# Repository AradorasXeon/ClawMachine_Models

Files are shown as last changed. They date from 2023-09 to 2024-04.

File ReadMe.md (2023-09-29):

Models are made in SCAD, STLs are also generated there.

GCodes are generated with Cura for ENDER3 printer (not V2, not some fancy version, but probably would work on any of those).

License: MIT License

Copyright (c) 2023 Krisztián József Varga

Permission is hereby granted, free of charge, to any person obtaining a copy
of this software and associated documentation files (the "Software"), to deal
in the Software without restriction, including without limitation the rights
to use, copy, modify, merge, publish, distribute, sublicense, and/or sell
copies of the Software, and to permit persons to whom the Software is
furnished to do so, subject to the following conditions:

The above copyright notice and this permission notice shall be included in all
copies or substantial portions of the Software.

THE SOFTWARE IS PROVIDED "AS IS", WITHOUT WARRANTY OF ANY KIND, EXPRESS OR
IMPLIED, INCLUDING BUT NOT LIMITED TO THE WARRANTIES OF MERCHANTABILITY,
FITNESS FOR A PARTICULAR PURPOSE AND NONINFRINGEMENT. IN NO EVENT SHALL THE
AUTHORS OR COPYRIGHT HOLDERS BE LIABLE FOR ANY CLAIM, DAMAGES OR OTHER
LIABILITY, WHETHER IN AN ACTION OF CONTRACT, TORT OR OTHERWISE, ARISING FROM,
OUT OF OR IN CONNECTION WITH THE SOFTWARE OR THE USE OR OTHER DEALINGS IN THE
SOFTWARE.

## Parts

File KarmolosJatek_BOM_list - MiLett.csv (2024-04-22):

 |  | Honnan Rendeltem | Megnevezés | Link | Méret ha van | DB szám
Egy csomó szerszámot is vettem, de ezeket későbbi projektekhez is részben, csak sok volt, ami most kellett először, azokat nem listázom ide. |  | Model elveszett | X_tarto-Y-kocsira | 3D nyomtatni |  | 1
Ezenkívül voltak dolgok, amikből többet vettem, de a darabszámnál a felhasznált mennyiség került feltüntetésre, az árhoz azt írtam be, amibe nekem megrendeléskor az adott mennyiség került. |  | Model elveszett | X_tarto-Y-tengelyre_LM8uu | 3D nyomtatni |  | 1
Figyelembe véve a projekt hosszúságát, és hogy mennyire későn kezdtem neki ennek a BOM listának, a dokumentáció nem teljes körű. Itt ott kisebb nagyobb eltérések lehetnek benne. |  | Model elveszett | TekercseloMOtorTarto | 3D nyomtatni |  | 1
 |  | Model feltöltve | TekercseloTarcsa | 3D nyomtatni |  | 1
árak (2023.09.16) rendeléskor februárban lehet olcsóbb volt... |  |  |  |  |  | 1
 | 4 017 Ft | OBI | MDF lap 8 mm (hátlap) | 0,59075 | 850x695 | 1
 | 3 361 Ft | OBI | MDF lap 8 mm (top box alja) | 0,4942 | 700x706 | 1
 |  | OBI | HDF fedo 8 | 0,42575 | 650x655 | 1
 | 3 270 Ft | OBI | MDF alja + legalja (300×261) 8 | 0,48094 | 692x695 | 1 | Ez végül külön tétel volt, bár az egyik kivágást én csináltam
Sajnos nem találom a weblapon már a konkrét típust, de ha jól emlékszem ez már akkor se ment 3500 Ft/m körül mozgott az ára, ha jól emlékszem + vágás díja volt, 3600 / m-rel számolok |  | OBI | Deszka (20x100) | 2,8 | 700 | 4
 | 9 504 Ft | OBI | Deszka (20x100) | 2,64 | 660 | 4
 | 1 566 Ft | OBI | Deszka (20x100) | 0,435 | 435 | 1
 | 1 019 Ft | OBI | Deszka (20x100) | 0,283 | 283 | 1
 | 2 408 Ft | OBI | Deszka (20x100) | 0,669 | 669 | 1
 | 997 Ft | OBI | Deszka (20x100) | 0,277 | 277 | 1
 | 1 328 Ft | OBI | Deszka (20x100) | 0,369 | 369 | 1
ennek anno felírtam h 38 ezer a kettő együtt | 17 717 Ft | OBI | Plexi | https://www.obi.hu/muanyag-tetok/gutta-lemez-2-5-mm-polisztirol-sima-200-cm-x-100-cm-atlatszo/p/3230216 | 700x850 | 3 | front az 1-ikből vágva | https://www.obi.hu/muanyag-tetok/gutta-lemez-2-5-mm-polisztirol-sima-200-cm-x-100-cm-atlatszo/p/3230216 | ez: 1*2 m-es verzióban | vastagság: 2,5 mm |  | =>9,2 kg
De kivágások miatt ebből úgyis kell 2 db |  | OBI | Plexi |  | 263x142 | 1 |  |  | ebből 2 db kellett ~38 000 Ft
 |  | OBI | Plexi |  | 300x142 | 1
 | 11 200 Ft | OBI | L profil 2020x10 |  | 1000 | 8 |  | https://www.praktiker.hu/csavar-zar-vasalat/vasalat-profilos-anyag/lemez-profil-szogvas/308666-dinocoop-l-profil-20x20x1-0-1m-szimmetrikus-alu-nyers | Ez kiderült, hogy van az OBI-ban is, csak én nem találtam valahogy, eredetileg 4 db volt az oszlophoz, de akkor még nem tudtam, hogy lehet hosszabb kiszerelésben is venni, akkor már olyanra csináltam volna, hogy teljesen végig érjen. A végeredmény azt hiszem 8 db 1 m-es volt, a 4 oszlopon kívül még ment a kiadó nyílsához kívülre és belülre is, illetve a plexi felső része is ragasztva lett ilyennel.
 | 560 Ft | OBI | Sarok Vas 2020 |  |  | 8 |  | https://www.obi.hu/sarokoesszekoetok-faoesszekoeto-vasak/szekszegletvas-sarga-horganyzott-25-mm-x-25-mm-x-14-mm/p/3098407
 | 256 Ft | OBI | HDF Irányító doboz (6 mm) | 0,05694 | 438 x 130 | 1 | teteje
 | 202 Ft | OBI | HDF Irányító doboz (6 mm) | 0,044928 | 432 x 104 | 1 | szemből lap
 | 57 Ft | OBI | HDF Irányító doboz (6 mm) | 0,01261 | 130 x 97 | 1 | jobb lap
 | 58 Ft | OBI | HDF Irányító doboz (6 mm) | 0,012896 | 124 x 104 | 1 | bal lap
 | 199 Ft | OBI | HDF Irányító doboz (6 mm) | 0,044304 | 426 x 104 | 1 | hátsólap
 | 226 Ft | OBI | HDF Irányító doboz (6 mm) | 0,050268 | 426 x 118 | 1 | alsőlap
ár rendeléskor (2023.02.19) |  |  | Kapaszkodo | 3D nyomtatni / vagy beszerezni vmi bútor áruházból |  | 2
 | 724 Ft | Caxtool | V-Slot 20x20 |  | 60 | 2
 | 3 496 Ft | Caxtool | Shaft_dia8 |  | 695 | 1
Nyugodtan rendelhettem volna onnan, figyelembe véve, hogy mekkora csúszásban volt végig a projekt... :D | 1 189 Ft | Variometrum | LM8UU | https://variometrum.hu/hu/linearis-golyos-csapagy-lme-tipus |  | 1 |  | talán
nincs raktáron - 1 db van + 1 T80-as, ebből végül volt olyan, amit 3D nyomtattam. | 5 468 Ft | Caxtool | GT2-6mm T60 bordáskerék 5 mm furat |  |  | 2
 | 6 722 Ft | Caxtool | Motor Mount Plate Nema 17 |  |  | 2 |  |  |  |  | Csavarok kellenek | × utáni rész a csavar hossza |  | nyílás m1 = hornyos csavar / kereszt hornyos csavar / belsőkulcsnyílűsú csavar (imbusz)
Ebből mind2 félét megrendeltem | 1 018 Ft | Caxtool | B6-M4 |  |  | 8 |  |  |  |  | 8 db B6-hoz | M4 × 15 (teljesen menetes, hengeres fej, nyílás m1), 1-2 mm-rel lehet hosszabb
 | 2 995 Ft | Caxtool | GT2 - 20T_Tension Pulley Without Teeth +603Z_dzino |  |  | 2 |  |  |  |  | 2 db a szíjfeszítőhöz 5-ös furat, minimum 20 mm hosszú csavar + anya esetleg alátét | M4 × 25 (vagy hosszabb, hengeres fej, nyílás m1)
 | 1 785 Ft | Caxtool | Joining Strip Plate 2 Hole |  |  | 2 |  |  |  |  | 4 db alátét a motor platekhez --> lehet maradhat az M4x10 akkor | 4 db sima alátét (lapos) M4-es csavarhoz
6 mm-es nem volt 1/4 inches (6,35 lett) | 194 Ft | Caxtool | Aluminium Spacer 6mm |  |  | 2 |  |  |  |  | 10 db M5 a kocsikhoz x10 minimum, de attól több ne is nagyon legyen | M5 × 10 (teljesen menetes, hengeres/sülyesztett fej, nyílás m1), 1-2 mm-rel lehet hosszabb
 | 23 350 Ft | Caxtool | Mini V Gantry Kit |  |  | 2 |  |  |  |  | 2 db M5, ami legalább 25 hosszú (oldalfalhoz rögzítés | M5 × 25 (vagy hosszabb, hengeres fej, nyílás m1)
 | 4 362 Ft | Caxtool | GT2-6mm bordásszíj |  | 3000 | 1 | 3m több mint elég (vmivel több, mint 1,2 m kell egy tengelyre) |  |  |  | 2 db M5-ös hernyó csavar legalább 20 hosszú ha van olyan, de ez talán 4-es tengellyel is lehet helyetesíteni | M5 × 20 (vagy hosszabb, hernyó csavar) --> ha nincs akkor M5-ös menetes szár és majd itthon elvágjuk
 |  | Csavar boltba majd | CSAVAROK Oldalt |  |  |  |  |  |  |  | 9 db M3-as csavar vagy kis tengely, a karomhoz | M3 × 15 (teljesen menetes, hengeres fej/ süllyesztett fej, nyílás m1), 1-2 mm-rel lehet hosszabb, de akkor kell mindegyikhez M3-as alátét is
 | 6 995 Ft | Caxtool | V-Slot 20x20 |  | 580 | 2
 |  |  |  |  |  |  |  |  |  |  |  | M3 × 7 (teljesen menetes, hengeres fej, nyílás m1), 1-2 mm-rel lehet hosszabb, de akkor kell mindegyikhez M3-as alátét is
 |  | Csavarok és szögek
 |  |  | 3,5 - es facsavarokból vettem egy nagy csomagot, abból sok kellett
 |  |  | Kicsi szögeket vettem, az MDF lapok felszögelve lettek a deszkákból készült vázakra. |  |  |  |  |  |  |  | SATU | 2 db M4-es anya
 |  |  |  |  |  |  |  |  |  |  |  | 9 db M3-as anya
 |  |  | AliExpress / Banggood
 | 275 Ft | AliExpress | Fő nyomó gomb (30 mm Blue) | https://www.aliexpress.com/item/1005003087221149.html?spm=a2g0o.cart.0.0.a8de38davfa4l7&mp=1 |  | 1 |  |  |  |  |  |  | 9 | M3 × 15 (teljesen menetes, hengeres fej/ süllyesztett fej, nyílás m1), 1-2 mm-rel lehet hosszabb, de akkor kell mindegyikhez M3-as alátét is
 | 1 250 Ft | AliExpress | Irányító kar (Blue) | https://www.aliexpress.com/item/32827286314.html?spm=a2g0o.cart.0.0.a8de38davfa4l7&mp=1 |  | 1 |  |  |  |  |  |  | 8 | M4 × 15 (teljesen menetes, hengeres fej, nyílás m1), 1-2 mm-rel lehet hosszabb
 | 18 200 Ft | AliExpress | Karom (L-es) | https://www.aliexpress.com/item/1005003908251157.html |  | 1 |  |  |  |  |  |  | 2 | M4 × 25 (vagy hosszabb, hengeres fej, nyílás m1)
 | 525 Ft | AliExpress | Tápkábel csatlakozó (AC-17) | https://www.aliexpress.com/item/1005002516320900.html |  | 1 |  |  |  |  |  |  | 10 | M5 × 10 (teljesen menetes, hengeres/sülyesztett fej, nyílás m1), 1-2 mm-rel lehet hosszabb
 | 2 856 Ft | AliExpress | LED szalag (~2,4 m felhasználva/ white PCB, 3 m 30 IP30 China) | https://www.aliexpress.com/item/32682015405.html |  | 1 |  |  |  |  |  |  | 2 | M5 × 25 (vagy hosszabb, hengeres fej, nyílás m1)
ebből nem lett minden motor felhasználva --> végül se a shield, se a driverek, se az uno klón nem lett felhasználva csak két motor erős kerekítés: | 6 598 Ft | Banggood | Stepper motorok, arduino klón, cnc shield | https://hu.banggood.com/TWO-TREES-CNC-Shield-+-UNO-R3-Board-+4x-A4988-Stepper-Motor-Driver-+4x-4401-Stepper-Motor-Kit-for-3D-Printer-p-1510212.html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 |  | 1 |  |  |  |  |  |  | 2 | M5 × 20 (vagy hosszabb, hernyó csavar) --> ha nincs akkor M5-ös menetes szár és majd itthon elvágjuk
 | 11 399 Ft | Banggood | 400 W-os táp | https://hu.banggood.com/Geekcreit-AC-110-240V-Input-To-DC-24V-17A-400W-Switching-Power-Supply-Driver-Board-p-1272112.html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 |  | 1 |  |  |  |  |  |  | 2 | M4 anya
 |  |  |  |  |  |  |  |  |  |  |  |  | 9 | M3 anya
 |  |  | HESTORE |  |  |  |  |  |  |  |  |  | 4 | M4 alátét (sima = lapos)
 | 125 Ft | HESTORE | Saru | https://www.hestore.hu/prod_10023274.html |  | 5
 | 199 Ft | HESTORE | Szemes csatlakozóvég | https://www.hestore.hu/prod_10023978.html |  | 7
 | 510 Ft | HESTORE | Mikrokapcsoló | https://www.hestore.hu/prod_10036149.html |  | 4
 | 1 603 Ft | HESTORE | Szigetelt mérővezeték | https://www.hestore.hu/prod_10035265.html |  | 2
 | 867 Ft | HESTORE | LM338T | https://www.hestore.hu/prod_10026081.html |  | 2
 | 169 Ft | HESTORE | D882 | https://www.hestore.hu/prod_10043720.html |  | 1
 | 54 Ft | HESTORE | BY-299 | https://www.hestore.hu/prod_10026209.html |  | 1
 | 1 300 Ft | HESTORE | kék 0,35-ös vezeték | https://www.hestore.hu/prod_10035183.html |  | 12
 | 90 Ft | HESTORE | 1000 uF elektrolit kondenzátor | https://www.hestore.hu/prod_10028495.html |  | 1
Ami volt itthon az csak nagyjábóli öszeg, és összesítve vonatkozik! (nyílván nem 1 db ellenállás volt 400 Ft) | 400 Ft | volt itthon | ellenállások
 | 4 000 Ft | volt itthon | ARDUINO NANO klón
 | 600 Ft | volt itthon | Univerzális NYÁK
 | 100 Ft | volt itthon | pin sor
 | 200 Ft | volt itthon | 100 uF kondenzátor
 | 100 Ft | volt itthon | jumper kábelek, amiket szétvagdostam
 | 244 Ft | HESTORE | PCB sorkapocs 2,5 mm^2 (így is kicsi volt) | https://www.hestore.hu/prod_10043373.html |  | 2
 | 416 Ft | AliExpress | DCDC konverter (5 db / csomag) | https://www.aliexpress.com/item/1852412352.html |  | 1 | ===> lehet 12 V-oshoz is ezt rakom majd
 | 3 150 Ft | AliExpress | Arduino NANO klón | https://www.aliexpress.com/item/1005005594272986.html |  | 2
 | 8 510 Ft | AliExpress | Stepper motor PG 14 (gear box ratio 1:14) | https://www.aliexpress.com/item/1005001670848546.html |  | 1
 | 372 Ft | HESTORE | LM386N végfokozat erősítő | https://www.hestore.hu/prod_10021938.html |  | 2
 | 212 Ft | HESTORE | Hangszóróvezeték, 2 x 0,35 mm2, piros-fekete, rézbevonatú alumínium sodrat | https://www.hestore.hu/prod_10024846.html |  | 3
 | 960 Ft | HESTORE | Univerzális hangszóró 1W / 8 Ohm / 66mm | https://www.hestore.hu/prod_10026559.html |  | 2
 | 280 Ft | HESTORE | Tömör vezeték (táp ellátással kapcsolatos) | https://www.hestore.hu/prod_10034881.html |  | 2
kb. link csak reprezentatív | 3 600 Ft | volt itthon | joystick & gomb összekötő vezetékek kb.: 8 × 3 m | https://www.hestore.hu/prod_10044686.html |  | 24
 | 6 000Ft | AliExpress | Stepper Driver | https://www.aliexpress.com/item/1005005967708477.html |  | 3
Kb.: | 1 500Ft | AliExpress | GT2 Timing Belt Pulley | https://www.aliexpress.com/item/1005004839169588.html |  | 1
Nagyjábóli összeg | 192 908 Ft | azóta volt infláció stb, és a failed atamptek nincsenek beleszámolva

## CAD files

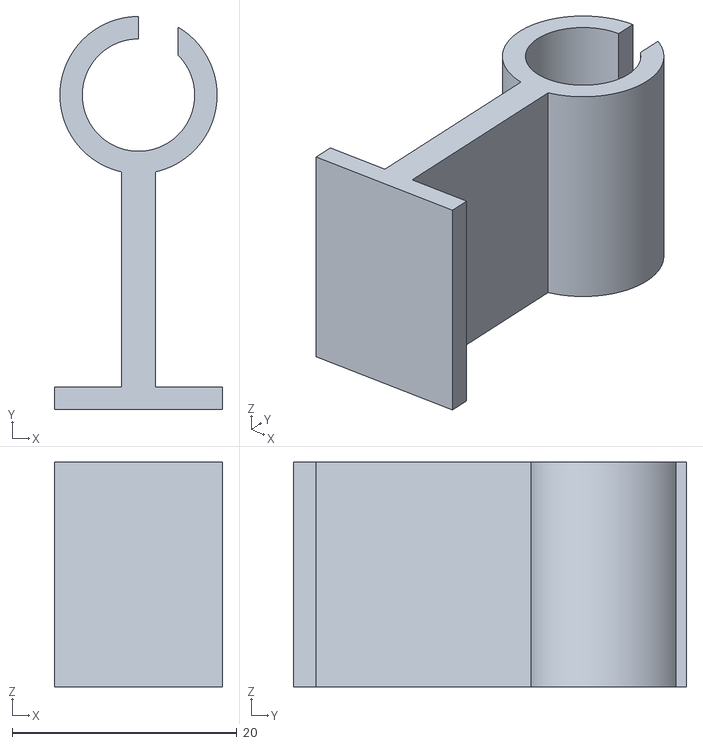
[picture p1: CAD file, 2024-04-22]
STL/WireHolder_RingPillar.stl
15.0 x 35.0 x 20.0

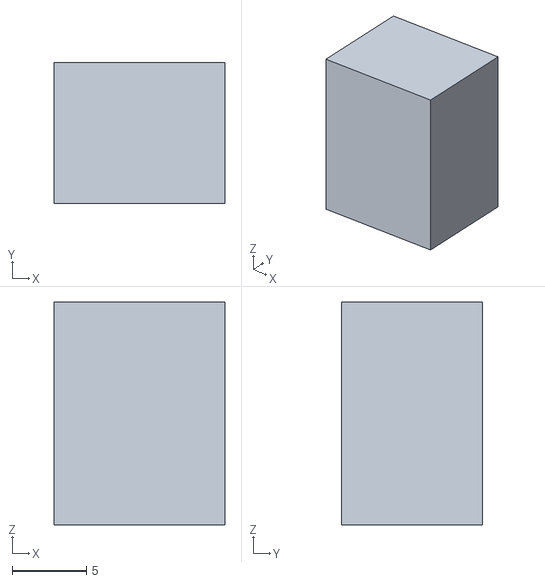
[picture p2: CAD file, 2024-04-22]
STL/LimiterCollider_addon.stl
11.5 x 9.50 x 15.0

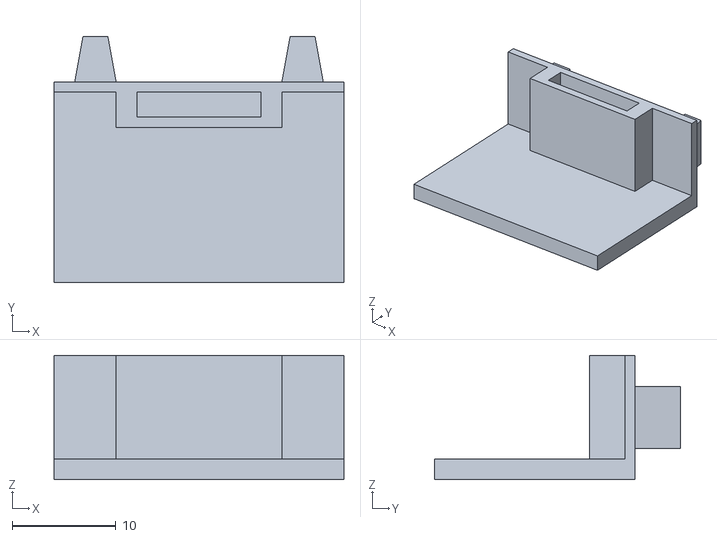
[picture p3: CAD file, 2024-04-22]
STL/Claw_Box_Belt_onlyPassingHalf.stl
28.0 x 23.8 x 12.0

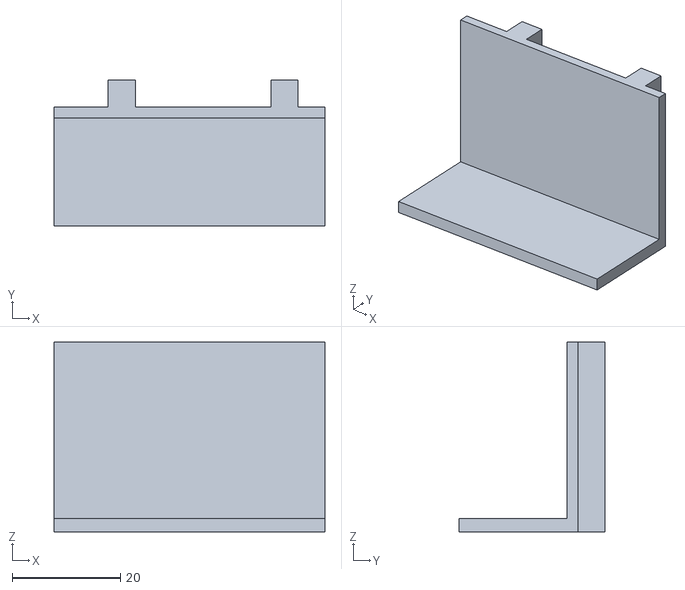
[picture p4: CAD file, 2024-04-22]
STL/Stepper_Driver_StandOff_part2.stl
50.0 x 27.0 x 35.0

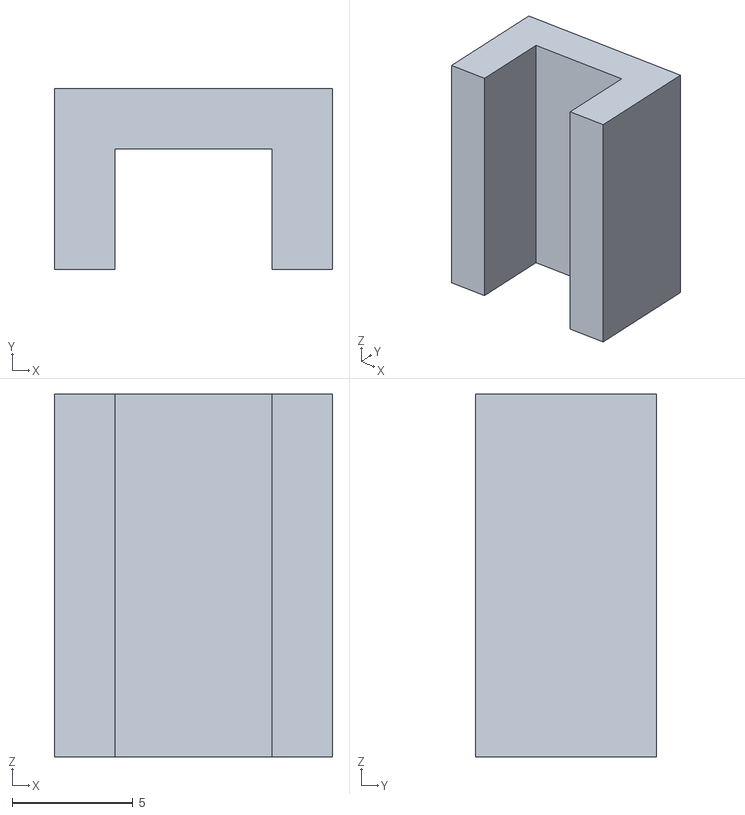
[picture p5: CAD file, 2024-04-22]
STL/LimiterCollider.stl
11.5 x 7.50 x 15.0

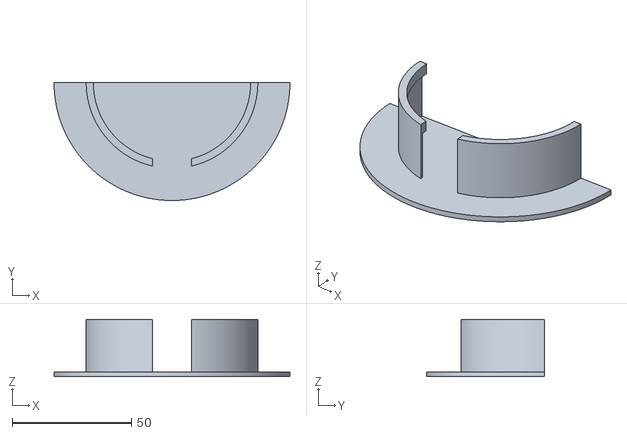
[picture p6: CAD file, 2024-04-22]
STL/Speaker_holder.stl
99.0 x 49.5 x 24.0

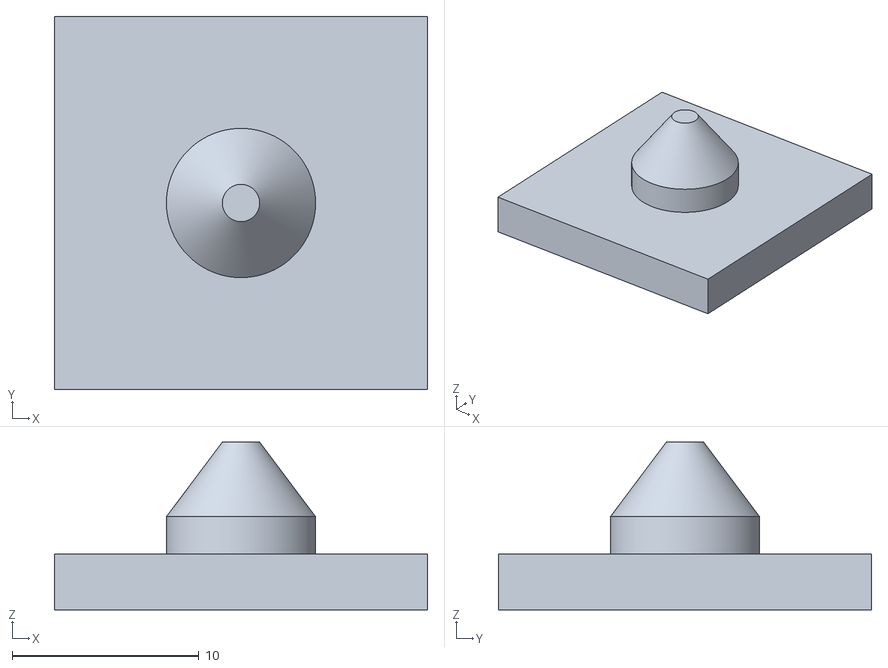
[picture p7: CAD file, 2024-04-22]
STL/Stepper_Driver_StandOff.stl
20.0 x 20.0 x 9.00

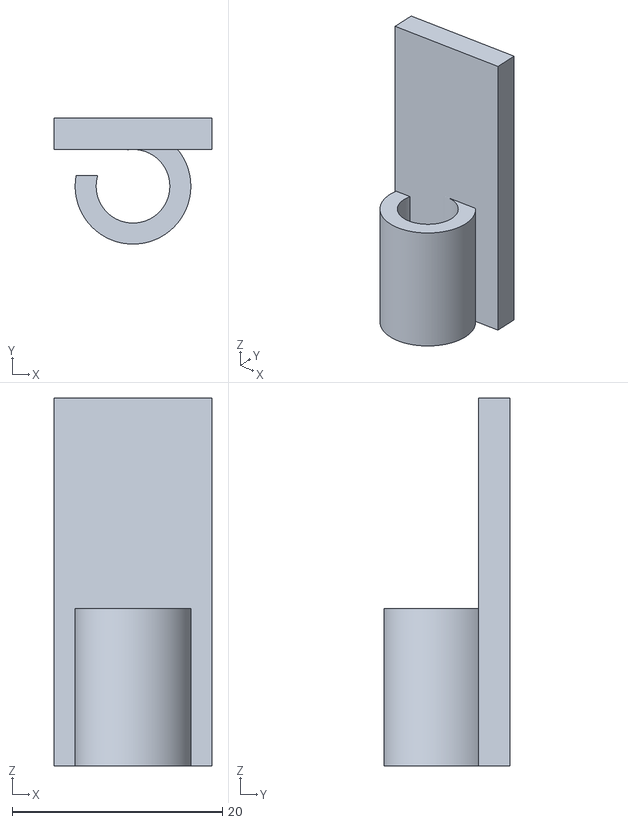
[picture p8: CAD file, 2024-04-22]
STL/WireHolder_RingDown.stl
15.0 x 12.0 x 35.0

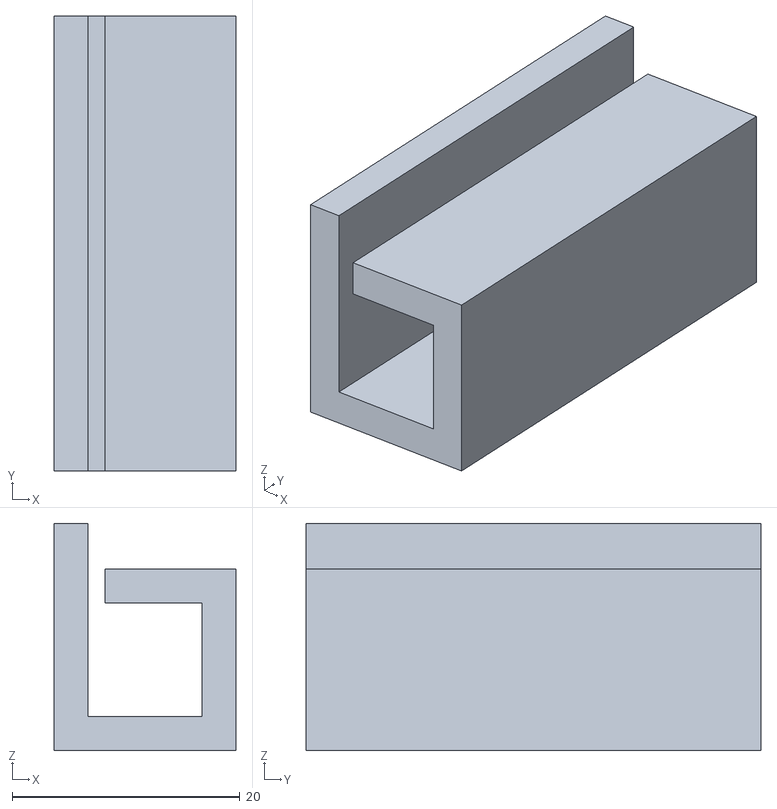
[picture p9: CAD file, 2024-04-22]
STL/WireHolder_Wall.stl
16.0 x 40.0 x 20.0

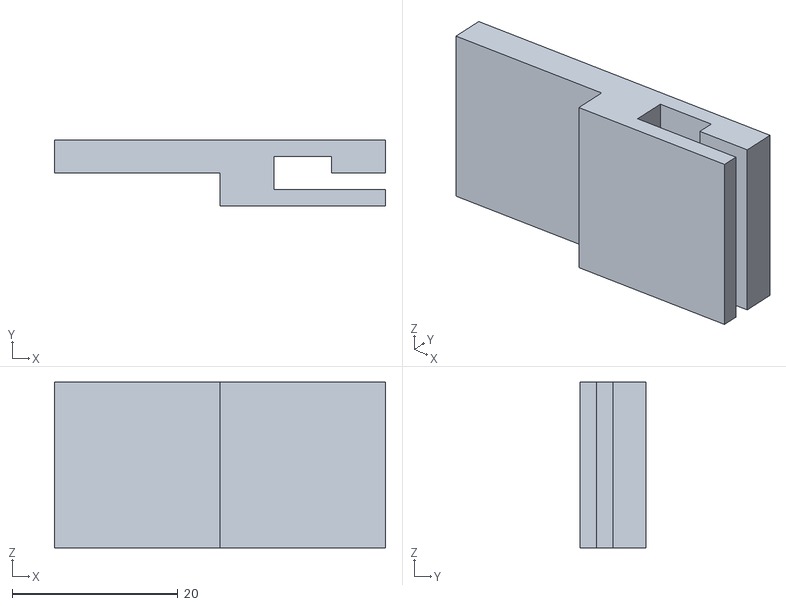
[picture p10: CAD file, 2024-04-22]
STL/4WireHolder.stl
40.0 x 8.00 x 20.0

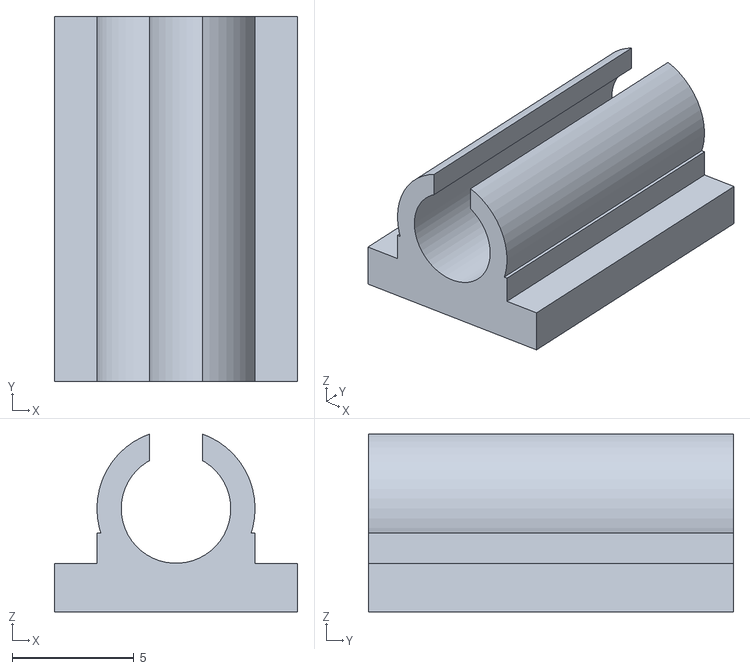
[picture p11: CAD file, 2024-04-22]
STL/WireHolder.stl
10.0 x 15.0 x 7.31

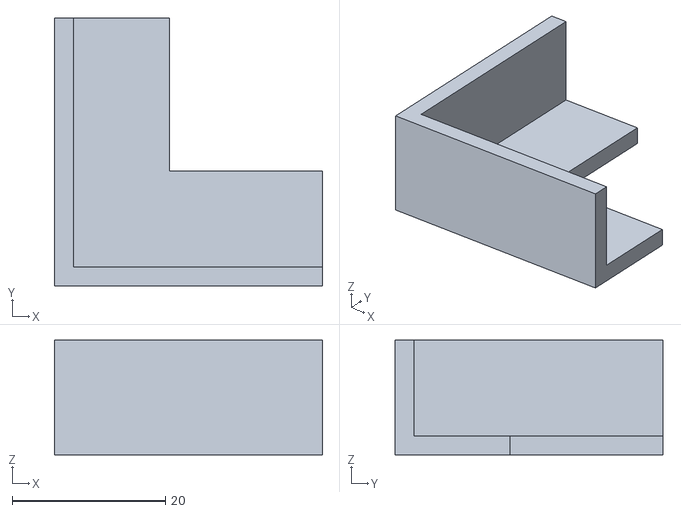
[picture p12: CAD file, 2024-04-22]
STL/Anti-Slip_Corners.stl
35.0 x 35.0 x 15.0

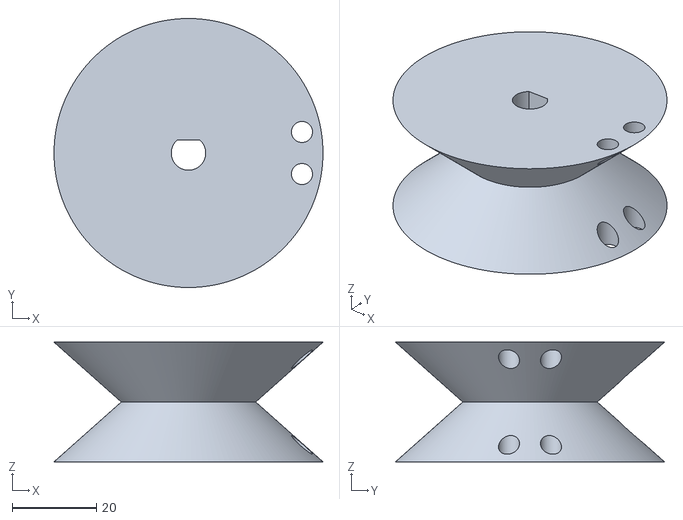
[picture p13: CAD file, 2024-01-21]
STL/ClawDrumV4.stl
64.0 x 64.0 x 28.4

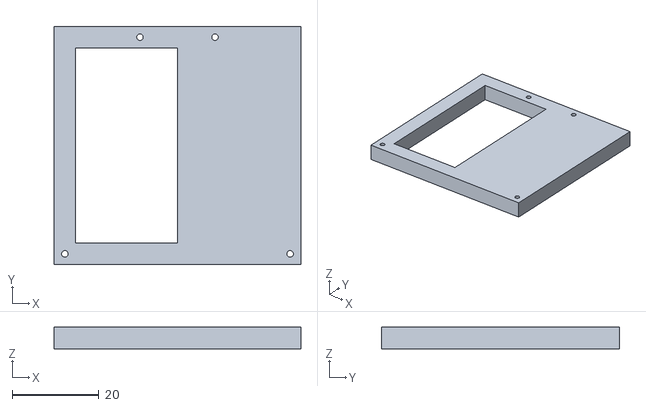
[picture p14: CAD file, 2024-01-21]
STL/ClawDrumMotorHolderLid.stl
57.0 x 55.0 x 5.00

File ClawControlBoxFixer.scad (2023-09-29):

cube([15,15,2]);

translate([0,17,0])rotate([90,0,0])cube([15,17,2]);
rib();
translate([13,0,0])rib();


module rib()
{
translate([2,0,0])
rotate([0,-90,0])
linear_extrude(2)
{
polygon([[0,0],[0,17],[17,17]]);   
}
}

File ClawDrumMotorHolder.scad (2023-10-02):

$fn=150;
MOTOR_WIDTH = 45; //width of square with safety
MOTOR_LENGTH = 47;//length of the motor house without PG
PG_DIA = 37; //diameter of the engine with safety

WALL_WIDTH = 5;
ALLAN_HOLE_DIA = 5.5;
ALLAN_DISTANCE = 10;
SELF_TAPPING_DIA = 2.8; //for M3×16 screws

difference()
{
union()
{
difference()
{
	cube([MOTOR_WIDTH, MOTOR_LENGTH, WALL_WIDTH]);
	translate([MOTOR_WIDTH/2,MOTOR_LENGTH/2,0])AllenHoles(ALLAN_DISTANCE, ALLAN_HOLE_DIA, WALL_WIDTH);
	
}
translate([0,MOTOR_LENGTH,0])BackWall(WALL_WIDTH, MOTOR_WIDTH);
translate([0,-WALL_WIDTH,0])FrontWall(WALL_WIDTH, MOTOR_WIDTH, PG_DIA);
difference()
{
	translate([0,0,WALL_WIDTH+MOTOR_WIDTH])cube([MOTOR_WIDTH, MOTOR_LENGTH, WALL_WIDTH]);
	translate([MOTOR_WIDTH/2,MOTOR_LENGTH/2,WALL_WIDTH+MOTOR_WIDTH])cylinder(h = WALL_WIDTH, d = 1.28*(2*ALLAN_DISTANCE+ALLAN_HOLE_DIA));
}
translate([-WALL_WIDTH,-WALL_WIDTH,0])SideWall(WALL_WIDTH, MOTOR_LENGTH, MOTOR_WIDTH);
}
SideHoles(MOTOR_WIDTH, MOTOR_LENGTH, WALL_WIDTH, SELF_TAPPING_DIA);


}

module AllenHoles(dist, hole, depth)
{
	cylinder(h = depth, d = hole);
	translate([0,dist,0])cylinder(h = depth, d = hole);
	translate([0,-dist,0])cylinder(h = depth, d = hole);
	translate([dist,0,0])cylinder(h = depth, d = hole);
	translate([-dist,0,0])cylinder(h = depth, d = hole);
}

module BackWall(wall, side)
{
	cube([side, wall, 2*wall+side]);
}

module FrontWall(wall, side, pgDia)
{
	dia = 1.05*pgDia;
	difference()
	{
		BackWall(wall, side);
		translate([side/2,0,wall+side/2])rotate([0,90,90])cylinder(h = wall, d = dia);
		translate([side/2,0,wall+side/2-dia/2])cube([side,wall,dia]);
	}
}

module SideWall(wall, length, baseHeight)
{
	cube([wall, length+2*wall, baseHeight+2*wall]);
}

module SideHoles(side, length, wall, hole)
{
	depth = 6*hole;
	origin = [side,-wall/2,wall/2];
	
	translate(origin)rotate([0,-90,0])cylinder(h = depth, d = hole);
	translate(origin+[0,0,side+wall])rotate([0,-90,0])cylinder(h = depth, d = hole);
	translate(origin+[0,length+wall,side+wall])rotate([0,-90,0])cylinder(h = depth, d = hole);
	translate(origin+[0,length+wall,0])rotate([0,-90,0])cylinder(h = depth, d = hole);
}

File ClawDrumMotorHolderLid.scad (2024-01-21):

$fn=50;
MOTOR_WIDTH = 45; //width of square with safety
MOTOR_LENGTH = 47;//length of the motor house without PG
PG_DIA = 37; //diameter of the engine with safety

WALL_WIDTH = 5;
ALLAN_HOLE_DIA = 5.5;
ALLAN_DISTANCE = 10;
SELF_TAPPING_DIA = 1.5; //for M3×16 screws, maybe for M2 instead?

difference()
{
cube([MOTOR_LENGTH+2*WALL_WIDTH, MOTOR_WIDTH+2*WALL_WIDTH, WALL_WIDTH]);
translate([WALL_WIDTH,WALL_WIDTH,0])cube([MOTOR_LENGTH/2, MOTOR_WIDTH, WALL_WIDTH]);
SideHoles(MOTOR_WIDTH, MOTOR_LENGTH, WALL_WIDTH, SELF_TAPPING_DIA);
}

module SideHoles(side, length, wall, hole)
{
	depth = wall;
	origin = [wall/2,wall/2,0];
	
	translate(origin)cylinder(h = depth, d = hole);
	translate(origin+[length+wall,0,0])cylinder(h = depth, d = hole);
	translate(origin+[(length+wall)*1/3,side+wall,0])cylinder(h = depth, d = hole);
	translate(origin+[(length+wall)*2/3,side+wall,0])cylinder(h = depth, d = hole);
	
}

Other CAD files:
STL/PCB_StandOff_sturdy.stl
STL/ClawDrumMotorHolder.stl
STL/PCB_1_hole_StandOff.stl
STL/ClawPistonCollider.stl
Stepper_Driver_StandOff.scad
4WireHolder.scad
Anti-Slip_Corners.scad
ArduinoUno_1_hole_StandOff.scad
ClawBeam.scad
ClawBeamCLAW.scad
ClawBeamCLAW_V2.scad
ClawBeamV2.scad
ClawDrum.scad
ClawDrumV2.scad
ClawDrumV3.scad
ClawHandle.scad
ClawLimitSwitch_X_Left.scad
ClawLimitSwitch_X_Right.scad
ClawLimitSwitch_Y.scad
ClawLongPIllarHelper.scad
ClawMagnetHolder.scad
ClawMagnetHolderV2.scad
ClawMagnetHolderV3.scad
ClawPiston.scad
ClawPistonCollider.scad
ClawPistonColliderV2.scad
ClawPistonV2.scad
ClawPowerSupplyHolderV1.scad
ClawShortPillarCover.scad
ClawShortPillarCover_concave.scad
Claw_Box_Belt.scad
Claw_Box_Belt_onlyPassingHalf.scad
LimiterCollider.scad
LimiterCollider_addon.scad
PCB_1_hole_StandOff.scad
PCB_StandOff_sturdy.scad
STL/ArduinoUno_1_hole_StandOff.stl
STL/ClawBeam.stl
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

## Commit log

2023-09-29 uploading files
    [ArduinoUno_1_hole_StandOff.scad, ArduinoUno_1_hole_StandOff.stl, ClawBeam.scad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]
2023-10-02 I printed with the ClawDrumHolder.gcode, bit it used a faulty stl, stl is fixed, other gcode not tested
    [ClawDrumMotorHolder.scad, ClawDrumMotorHolder.stl]
2024-01-21 added things from january
    [ClawDrumMotorHolderLid.scad, ClawDrumMotorHolderLid.stl, ClawDrumV3.scad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]
2024-04-22 mainly holders
    [4WireHolder.scad, 4WireHolder.stl, Anti-Slip_Corners.scad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]
2024-04-22 added prize calcutaion, for non 3D printed parts, SUM about: 195 000 HUF, failed attempts not calculated + ~1.5 year work
    [KarmolosJatek_BOM_list - MiLett.csv]
